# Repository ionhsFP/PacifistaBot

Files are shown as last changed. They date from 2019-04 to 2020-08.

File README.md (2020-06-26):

# PacifistaBot: Kit Humanoide de iniciación
PacifistaBot

Este Kit está pensado para todo aquel que quiera iniciarse en la competición de humanoides. Está diseñado con piezas estandarizadas, baratas, fácil de conseguir y pensado para ser de fácil montaje y programación. Está creado en su totalidad a base de impresión 3D, se programa desde un Arduino Nano y usa una placa controladora fácil de soldar.

Hay que destacar que el robot ha sido diseñado por OPRobots y han liberado las fuentes para que cualquiera pueda replicarlo, modificarlo o seguir desarrollándolo. Aunque su diseño inicial esté inspirado en los robots Pacifistas de la serie One Piece, el diseño es totalmente personalizable ya que tanto las manos y la cabeza, como los detalles decorativos de su pecho y piernas son totalmente modificables e intercambiables para conseguir un robot único.

Mediante este Kit se puede profundizar diferentes niveles de competencias técnicas, de las siguientes áreas STEM:

- Electrónica
- Mecatrónica
- Programación
- Dibujo
- Impresión 3D

El robot pacifistabot originalmente se ha diseñado para controlado por bluetooth. Partiendo de la idea original se ha modificado creando una nueva versión en la que se puede elegir controlarlo mediante bluetooth o mediante wifi (los 2 a la vez no se puede). En la siguiente tabla se puede ver la documentación de cada versión de robot.

| Pacifistabot | Pacifistabot-ESP | Pacifistabot-AlhII |
| --- | --- | --- |
| [Material y Equipos](./montaje/MATERIAL-EQUIPOS.md) | [Material y Equipos](./montaje/MATERIAL-EQUIPOS-ESPyBT.md) | [Material y Equipos](./montaje/MATERIAL-EQUIPOS-AlhII.md) |
| [Montaje y Calibración](./montaje/MONTAJE-CALIBRACION.md) | Montaje y Calibración | Montaje y Calibración |

El coste del material de montaje es inferior a 100 euros y para facilitar poder empezar a montar se ha documentado un listado de Material y Equipos necesarios. Clasificándolos por piezas 3D, componentes mecánicos, componentes electrónicos y equipos de trajo y herramientas.

Para guiar en el proceso de creación de robot, se ha documentado el proceso de Montaje y Calibración. En él se encuentra el proceso de montaje-ajustes mecánicos, montaje electrónico y calibración del robot.

Las especificaciones principales son:

DIMENSIONES

------

- Producto contraido: 320 x 220 x 160 mm
- Producto extendido: 450 x 600 x110 mm

PESO

------

- Producto: 1000 g ~

MATERIALES

------

- Piezas impresas en PLA o ABS
- Tornillos de acero inox.

COMPONENTES ELECTRÓNICOS

------

- 12 Servomotores MG 996R
- Bateria LiFe 6,6V 1100	mAh
- Controladora Arduino Nano
- Módulo Bluetooth hc-05
- Módulo Wifi ESP-01 (solo en Versión Pacifistabot-ESP)

COMUNICACIÓN

------

- Cable mini-Usb
- Bluetooth
- Wifi (solo en Versión Pacifistabot-ESP)
- Programación mediante OTA (Over The Air)(solo en Versión Pacifistabot-ESP)

SOFTWARE

------

- Programación: [Arduino IDE](https://www.arduino.cc/)
- Diseño electrónico: [Kicad](https://www.kicad-pcb.org/)
- Diseño mecánico: [Skeetup](https://www.sketchup.com/)
- Comunicacción: [Putty](https://www.putty.org) / [Arduino IDE](https://www.arduino.cc/) / [ScriptCommunicator](https://github.com/szieke/ScriptCommunicator_serial-terminal) /...
- APP android: [Bluetooth Electronics](https://www.keuwl.com/apps/bluetoothelectronics/) / [BlueTerm](https://play.google.com/store/apps/details?id=es.pymasde.blueterm&hl=en_US) / ...

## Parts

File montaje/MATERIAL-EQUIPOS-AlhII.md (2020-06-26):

# PacifistaBot AlhII: Material y Equipos
PacifistaBot

Dado que es un Kit de iniciación, uno de los puntos más importantes es que el material y equipos necesario para poderse montar no es muy complejo y es fácil de encontrar o de tener disponible. Se va a ir identificando los componentes para que los alumnos y profesores puedan ir gestionando la adquisición de ellos. Este es el materila necesario:

### Piezas 3D

Esta es la lista de piezas que hace falta para poder construir el robot humanoide PacifistaBot. Se necesita imprimir todas las piezas numeradas una sola vez, aunque hay que tener en cuenta que algunas de las piezas tienen varios diseños (por ejemplo la cabeza y las manos) a elegir. Los archivos podemos encontrarlos también en el repositorio de [OPRobots de piezas STL](https://github.com/robotaleh/PacifistaBot/tree/master/stl_files) preparadas para imprimirse en 3D o para poder realizar modificaciones gracias al [formato SketchUp](./../3d_model/PacifistaBot.skp). En este momento faltaría modificar el Torso para poder fijar mediante tornillos la placa PacifistaBot AlhII.

| Nº | Archivo | Descripción | Imagen |
| ---- | :---: | :---: | :---: |
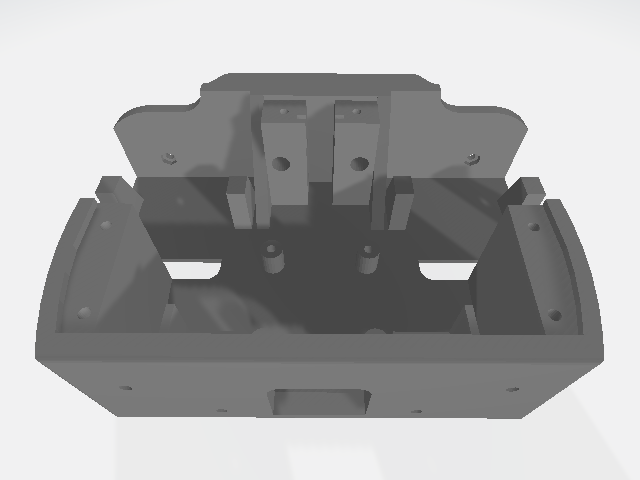
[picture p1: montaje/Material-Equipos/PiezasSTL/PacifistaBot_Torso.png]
| 1 | [PacifistaBot_Torso.stl](../stl_files/PacifistaBot_Torso.stl) | Pecho o caja torácica del robot. |  |
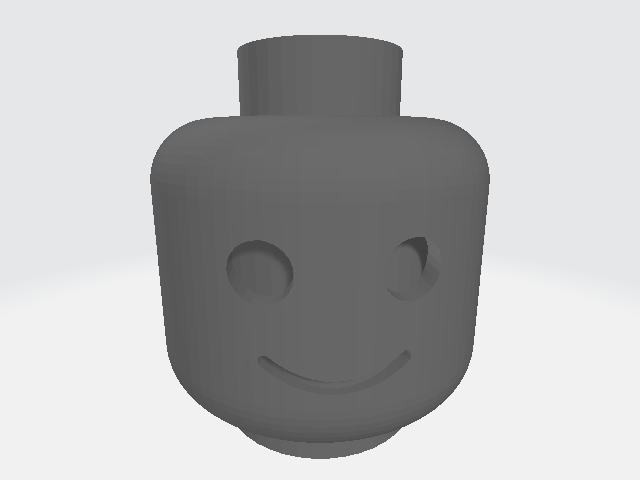
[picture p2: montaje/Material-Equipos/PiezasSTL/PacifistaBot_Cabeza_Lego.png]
| 2 | [PacifistaBot_Cabeza_Lego.stl](../stl_files/PacifistaBot_Cabeza_Lego.stl) | Cabeza hueca con forma muñeco de lego del robot |  |
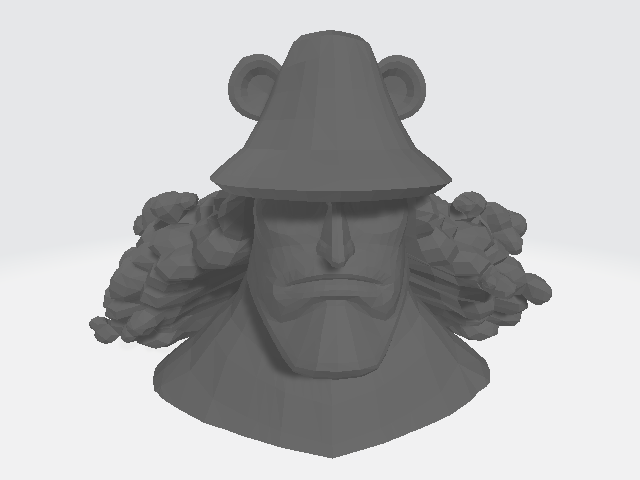
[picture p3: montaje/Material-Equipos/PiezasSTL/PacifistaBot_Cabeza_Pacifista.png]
| 2 | [PacifistaBot_Cabeza_Pacifista.stl](../stl_files/PacifistaBot_Cabeza_Pacifista.stl) | Cabeza maciza con forma de Pacifista de One Piece |  |
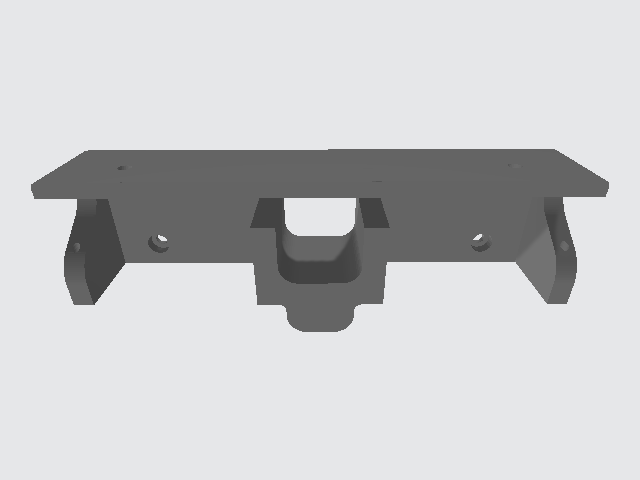
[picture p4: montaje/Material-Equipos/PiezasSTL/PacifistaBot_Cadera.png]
| 3 | [PacifistaBot_Cadera.stl](../stl_files/PacifistaBot_Cadera.stl) | Cadera del robot |   |
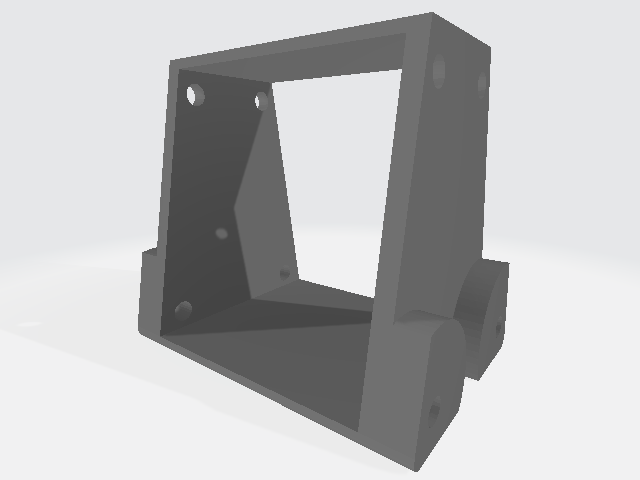
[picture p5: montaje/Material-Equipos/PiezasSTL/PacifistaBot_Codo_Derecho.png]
| 4 | [PacifistaBot_Codo_Derecho.stl](../stl_files/PacifistaBot_Codo_Derecho.stl) | Codo del brazo derecho del robot |  |
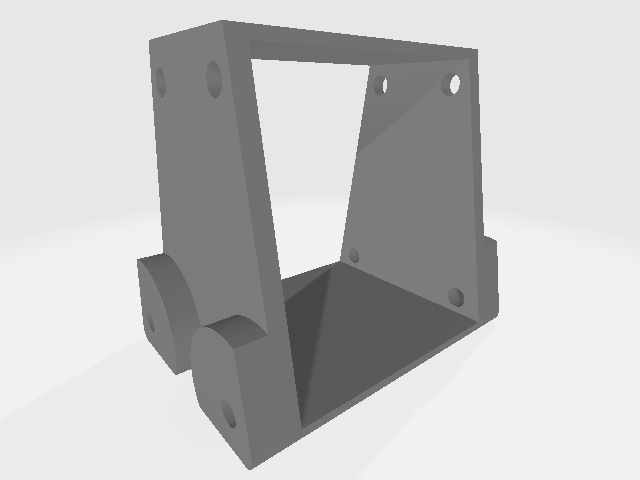
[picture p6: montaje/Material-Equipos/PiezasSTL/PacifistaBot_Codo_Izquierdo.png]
| 5 | [PacifistaBot_Codo_Izquierdo.stl](../stl_files/PacifistaBot_Codo_Izquierdo.stl) | Codo del brazo izquierdo del robot |  |
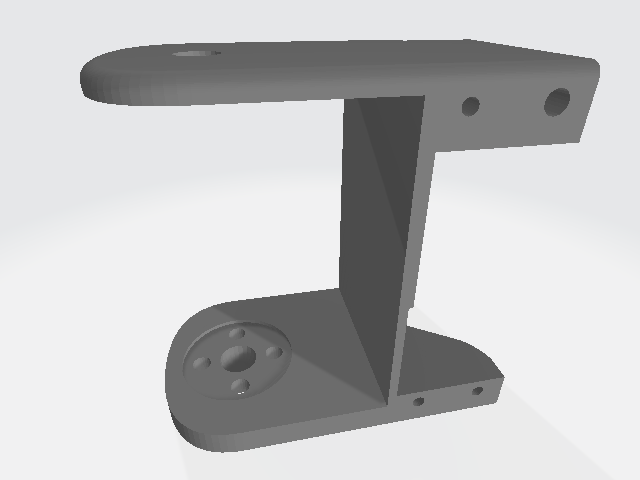
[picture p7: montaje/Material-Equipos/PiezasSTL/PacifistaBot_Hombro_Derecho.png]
| 6 | [PacifistaBot_Hombro_Derecho.stl](../stl_files/PacifistaBot_Hombro_Derecho.stl) | Hombro del brazo derecho del robot |  |
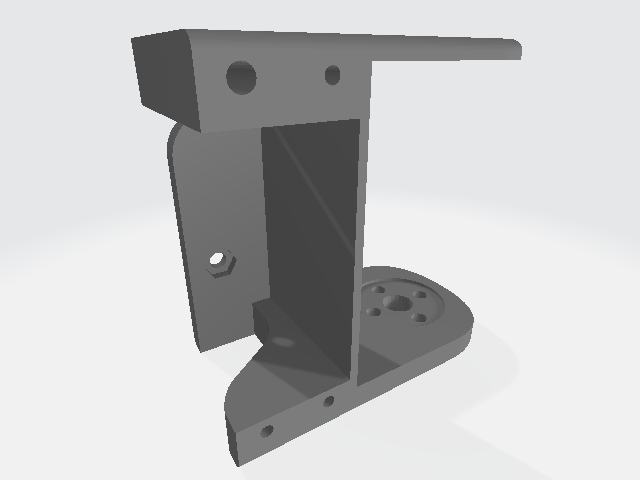
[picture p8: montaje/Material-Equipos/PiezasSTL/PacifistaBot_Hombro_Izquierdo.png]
| 7 | [PacifistaBot_Hombro_Izquierdo.stl](../stl_files/PacifistaBot_Hombro_Izquierdo.stl) | Hombro del brazo izquierdo del robot |  |
| 8 | [PacifistaBot_Ingle_Derecha.stl](../stl_files/PacifistaBot_Ingle_Derecha.stl) | Ingle de la pierna derecha del robot |  |
| 9 | [PacifistaBot_Ingle_Izquierda.stl](../stl_files/PacifistaBot_Ingle_Izquierda.stl) | Ingle de la pierna izquierda del robot |  |
| 10 | [PacifistaBot_Link_Frontal_Inferior_Derecho.stl](../stl_files/PacifistaBot_Link_Frontal_Inferior_Derecho.stl) | Espinilla de la pierna derecha del robot |  |
| 11 | [PacifistaBot_Link_Frontal_Inferior_Izquierdo.stl](../stl_files/PacifistaBot_Link_Frontal_Inferior_Izquierdo.stl) | Espinilla de la pierna izquierda del robot |  |
| 12 | [PacifistaBot_Link_Frontal_Superior_Derecho.stl](../stl_files/PacifistaBot_Link_Frontal_Superior_Derecho.stl) | Cuádriceps femoral del muslo de la pierna derecha del robot  |  |
| 13 | [PacifistaBot_Link_Frontal_Superior_Izquierdo.stl](../stl_files/PacifistaBot_Link_Frontal_Superior_Izquierdo.stl) | Cuádriceps femoral del muslo de la pierna izquierda del robot |  |
| 14 | [PacifistaBot_Link_Mano_Inferior_Frontal_Brazo _Derecho.stl](../stl_files/PacifistaBot_Link_Mano_Inferior_Frontal_Brazo_Derecho.stl) | Antebrazo palmar frontal derecho del robot |  |
| 15 | [PacifistaBot_Link_Mano_Inferior_Frontal_Brazo _Izquierdo.stl](../stl_files/PacifistaBot_Link_Mano_Inferior_Frontal_Brazo_Izquierdo.stl) | Antebrazo palmar frontal izquierdo del robot |  |
| 16 | [PacifistaBot_Link_Mano_Inferior_Trasero_Brazo _Derecho.stl](../stl_files/PacifistaBot_Link_Mano_Inferior_Trasero_Brazo_Derecho.stl) | Antebrazo palmar trasero derecho del robot |  |
| 17 | [PacifistaBot_Link_Mano_Inferior_Trasero_Brazo _Izquierdo.stl](../stl_files/PacifistaBot_Link_Mano_Inferior_Trasero_Brazo_Izquierdo.stl) | Antebrazo palmar trasero izquierdo del robot |  |
| 18 | [PacifistaBot_Link_Mano_Superior_Brazo _Derecho.stl](../stl_files/PacifistaBot_Link_Mano_Superior_Brazo_Derecho.stl) | Antebrazo supinador derecho del robot |  |
| 19 | [PacifistaBot_Link_Mano_Superior_Brazo _Izquierdo.stl](../stl_files/PacifistaBot_Link_Mano_Superior_Brazo_Izquierdo.stl) | Antebrazo supinador izquierdo del robot |  |
| 20 | [PacifistaBot_Link_Servo_Inferior_Frontal_Brazo _Derecho.stl](../stl_files/PacifistaBot_Link_Servo_Inferior_Frontal_Brazo_Derecho.stl) | Triceps frontal del brazo derecho del robot |  |
| 21 | [PacifistaBot_Link_Servo_Inferior_Frontal_Brazo _Izquierdo.stl](../stl_files/PacifistaBot_Link_Servo_Inferior_Frontal_Brazo_Izquierdo.stl) | Triceps frontal del brazo izquierdo del robot |  |
| 22 | [PacifistaBot_Link_Servo_Inferior_Trasero_Brazo _Derecho.stl](../stl_files/PacifistaBot_Link_Servo_Inferior_Trasero_Brazo_Derecho.stl) | Triceps trasero del brazo derecho del robot |  |
| 23 | [PacifistaBot_Link_Servo_Inferior_Trasero_Brazo _Izquierdo.stl](../stl_files/PacifistaBot_Link_Servo_Inferior_Trasero_Brazo_Izquierdo.stl) | Triceps trasero del brazo izquierdo del robot |  |
| 24 | [PacifistaBot_Link_Servo_Superior_Brazo _Derecho.stl](../stl_files/PacifistaBot_Link_Servo_Superior_Brazo_Derecho.stl) | Biceps del brazo derecho del robot |  |
| 25 | [PacifistaBot_Link_Servo_Superior_Brazo _Izquierdo.stl](../stl_files/PacifistaBot_Link_Servo_Superior_Brazo_Izquierdo.stl) | Biceps del brazo izquierdo del robot |  |
| 26 | [PacifistaBot_Link_Trasero_Inferior_Derecho.stl](../stl_files/PacifistaBot_Link_Trasero_Inferior_Derecho.stl) | Gemelo de la pierna derecha del robot |  |
| 27 | [PacifistaBot_Link_Trasero_Inferior_Izquierdo.stl](../stl_files/PacifistaBot_Link_Trasero_Inferior_Izquierdo.stl) | Gemelo de la pierna izquierda del robot |  |
| 28 | [PacifistaBot_Link_Trasero_Superior_Derecho.stl](../stl_files/PacifistaBot_Link_Trasero_Superior_Derecho.stl) | Biceps femoral de la pierna derecha del robot |  |
| 29 | [PacifistaBot_Link_Trasero_Superior_Izquierdo.stl](../stl_files/PacifistaBot_Link_Trasero_Superior_Izquierdo.stl) | Biceps femoral de la pierna izquierda del robot |  |
| 30 | [PacifistaBot_Mano_Lego_Derecha.stl](../stl_files/PacifistaBot_Mano_Lego_Derecha.stl) | Mano derecha con forma de muñeco de lego del robot |  |
| 31 | [PacifistaBot_Mano_Lego_Izquierda.stl](../stl_files/PacifistaBot_Mano_Lego_Izquierda.stl) | Mano izquierda con forma de muñeco de lego del robot |  |
| 30 | [PacifistaBot_Mano_Pacifista_Derecha.stl](../stl_files/PacifistaBot_Mano_Pacifista_Derecha.stl) |  Mano derecha con forma de Pacifista de One Piece del robot  |  |
| 31 | [PacifistaBot_Mano_Pacifista_Izquierda.stl](../stl_files/PacifistaBot_Mano_Pacifista_Izquierda.stl) | Mano izquierda con forma de Pacifista de One Piece del robot |  |
| 32 | [PacifistaBot_Muñeca_Derecha.stl](../stl_files/PacifistaBot_Muñeca_Derecha.stl) | Muñeca de la mano derecha del robot |  |
| 33 | [PacifistaBot_Muñeca_Izquierda.stl](../stl_files/PacifistaBot_Muñeca_Izquierda.stl) | Muñeca de la mano izquierda del robot |  |
| 34 | [PacifistaBot_Pie_Derecho.stl](../stl_files/PacifistaBot_Pie_Derecho.stl) | Pie derecho de la pierna derecha del robot |  |
| 35 | [PacifistaBot_Pie_Izquierdo.stl](../stl_files/PacifistaBot_Pie_Izquierdo.stl) | Pie izquierdo de la pierna derecha del robot |  |
| 36 | [PacifistaBot_Rodilla_Derecha.stl](../stl_files/PacifistaBot_Rodilla_Derecha.stl) | Rodilla de la pierna derecha del robot |  |
| 37 | [PacifistaBot_Rodilla_Izquierda.stl](../stl_files/PacifistaBot_Rodilla_Izquierda.stl) | Rodilla de la pierna izquierda del robot |  |
| 38 | [PacifistaBot_Tobillo_Derecho.stl](../stl_files/PacifistaBot_Tobillo_Derecho.stl) | Tobillo de la pierna derecha del robot |  |
| 39 | [PacifistaBot_Tobillo_Izquierdo.stl](../stl_files/PacifistaBot_Tobillo_Izquierdo.stl) | Tobillo de la pierna izquierda del robot |  |
| 40 | [PacifistaBot_Torso_Tapa.stl](../stl_files/PacifistaBot_Torso_Tapa.stl) | Tapa trasera del torso del robot |  |

### Componentes Mecánicos

A continuación se listan los componentes mecánicos necesarios para la construcción del robot PacifistaBot. Todos los componentes mecánicos y electrónicos son una evolución del robot PacifistaBot diseinado por [OPRobots](https://twitter.com/oprobots) por unos 100 euros, se va a ir identificando los componentes para que los alumnos y profesores puedan ir gestionando la adquisición de ellos. Junto al nombre de cada componente se ha puesto un link orientativo para poder tener una idea de donde comprar el componente. El número de tornillos deben sobrar algunos ya que los valores no están ajustados.

|  Nº  | Nombre/Compra | Descripción | Imagen |
| :--: | :---: | :---: | :---: |
|  12  | [Tornillo M3x8](https://es.aliexpress.com/wholesale?catId=0&initiative_id=SB_20190314011904&isPremium=y&SearchText=allen+m3x8) | Tornillo métrico allen cab. cilíndrica M3x8 |  |
|  33  | [Tornillo M3x10](https://es.aliexpress.com/wholesale?catId=0&initiative_id=SB_20190314011941&isPremium=y&SearchText=allen+m3x10) | Tornillo métrico allen cab. cilíndrica M3x10 |  |
|  35  | [Tornillo M3x16](https://es.aliexpress.com/wholesale?catId=0&initiative_id=SB_20190314012016&isPremium=y&SearchText=allen+m3x16) | Tornillo métrico allen cab. cilíndrica M3x16 |  |
|  10  | [Tornillo M3x25](https://es.aliexpress.com/wholesale?catId=0&initiative_id=SB_20190314012501&isPremium=y&SearchText=allen+m3x25) | Tornillo métrico allen cab. cilíndrica M3x25 (19 mm roscado) |  |
|  12  | [Servomotor](https://es.aliexpress.com/wholesale?catId=0&initiative_id=SB_20190314012523&isPremium=y&SearchText=MG996R) | Servomotor Tower pro MG996R corona metálica |  |
|  12  | [Accesorios servos](https://es.aliexpress.com/wholesale?catId=0&initiative_id=SB_20190314012523&isPremium=y&SearchText=MG996R) | Bolsa de varios accesorios de los servomotores. De la bolsa solo se usan los 4 tornillos roscados para amarrar los servomotres |  |
|  12  | [Disco engranado metálico](https://es.aliexpress.com/wholesale?catId=0&initiative_id=SB_20190314013124&isPremium=y&SearchText=MG996R+Disc) | Disco engranado metálico de los servomotores |  |
|  48  | [Tornillo M3x5](https://es.aliexpress.com/wholesale?catId=0&initiative_id=SB_20190314013124&isPremium=y&SearchText=MG996R+Disc) | Tornillos métricos philips de acero M3x5 para las pletinas metálicas |  |
|  70  | [Tuerca M3](https://es.aliexpress.com/wholesale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) | Tuercas autoblock M3 |  |
|  4 | [Alargadores](https://www.aliexpress.com/wholesale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) | Alargadores 21,5cm para los servomotores |  |

### Componentes Electrónicos

A continuación se listan los componentes electrónicos necesarios para la construcción del robot PacifistaBot-AlhII.  Junto al nombre de cada componente se ha puesto un link orientativo para poder tener una idea de donde comprar el componente. La placa original está diseñada por OPRobots y en esta versión se ha rediseñado adecuándola para hacerla funcionar mediante una Shield de la Alhambra II. La PCB está [diseñada por Don Bosco y Lasalle Berrozpe en Kicad](../pcb_files/Pacifista_AlhII) por lo que cualquiera puede consultar los esquemas y modificarlos. Se ha pasado el [esquema a PDF](../pcb_files/Pacifista_AlhII/Esquema_AlhII.pdf) para poder consultarlo sin necesidad de tener instalado Kicad. Además se han creado los [gerber del circuito Pacifistabot-AlhII](../pcb_files/Pacifista_AlhII/Gerbers) para que cualquiera pueda enviarlos a fabricar a alguno de los fabricantes como [pcbway](https://www.pcbway.com/), [seeedstudio](https://www.seeedstudio.com/fusion.html) ... (no me llevo comisión).

Esta placa puede comunicarse por Bluetooth (en la siguiente versión se espera poner wifi). Por lo que si se tiene claro la manera de comunicarse aparte del módulo, se puede ahorrar ciertos componentes.

|  Nº  | Nombre/Compra | Descripción | Imagen |
| :--: | :---: | :---: | :---: |
|  1 | PCB Pacifistabot AlhII |  Circuito impreso para la electrónica de control del robot.  |  |
|  1 | [Batería](https://hobbyking.com/es_es/zippy-flightmax-1100mah-6-6v-lifepo4-2s1p-receiver-pack.html) | Batería LiFe 2S 1100 mah 10C |  |
|  1 | [Alhambra II](https://alhambrabits.com/alhambra/) | Placa de FPGA Alhambra II |    |
|  1 | [Condensador](https://www.aliexpress.com/wholesale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) | Condensador de 16V y 1000uF |  |
|  1 | [Condensador](https://www.aliexpress.com/wholesale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) | Condensador de 6,3V y 820uF |  |
|  1 | [Bluetooth](https://www.aliexpress.com/wholesale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) (bt) | Módulo Bluetooth HC-05 6 pines y 1 botón |  |
|  1 | [Regulador dc-dc](https://www.aliexpress.com/wholesale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) | Regulador dc-dc MINI-360 con potenciómetro |  |
|  1 | [Tira de 8 pines](https://www.aliexpress.com/wholesale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) | Tira de pines paso 2.54 1x8 negro |  |
|  2 | [Tira de 6 pines](https://www.aliexpress.com/wholesale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) | Tira de pines paso 2.54 1x6 negro |  |
|  5 | [Tira de 6 pines](https://www.aliexpress.com/wholesale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) | Tira de pines paso 2.54 2x6pines negro, rojo y 1x6pines amarillo |    |
|  3 | [Tira de 2 pines](https://www.aliexpress.com/wholesale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) | Tira de pines paso 2.54 2 pines negro, rojo y amarillo |  |
|  1 | [Tira de 4 pines](https://www.aliexpress.com/wholesale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) | Tira de pines paso 2.54 1x4pines negro |  |
|  1 | [Tira de 6 pines hembra](https://www.aliexpress.com/wholesale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) | Tira de pines hembra paso 2.54 1x6pines negro |  |
|  2 | [Regleta 2 contactos](https://es.aliexpress.com/item/33002247818.html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,searchweb201602_,searchweb201603_) | Regleta para PCB con 2 contactos paso 2.54 |  |
|  1 | [Switch](https://es.aliexpress.com/item/33053285882.html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,searchweb201602_9,searchweb201603_53) | Interruptor KCD1 8A-250V |  |
|  2 | [Conectores faston](https://es.aliexpress.com/item/33004981765.html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,searchweb201602_9,searchweb201603_53) | Conector faston cable de 13cm |  |
|  1 | [Carrete de estaño](https://www.aliexpress.com/wholesale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) | Carrete de estaño para soldar |  |
|  1 | [Cable microUSB](https://es.aliexpress.com/wholesale?catId=0&initiative_id=SB_20200626011051&SearchText=microusb+usb) | Cable microUSB |  |

### Equipos y herramientas

Esta es la lista de equipos y herramientas necesarias tanto para el montaje como para el uso y mantenimiento del robot. En la lista aparece lo recomendado algunos no son obligatorios(Tienen un guión "-" en el nombre) o varios tinen la misma función (Tienen un asterisko y un nombre "*1" en el nombre).

|  Nº  | Nombre | Descripción | Imagen |
| :--: | :---: | :---: | :---: |
|  1 | Llave allen | Llave allen de 1,5 |  |
|  1 | Destornillador philips | Destornillador philips de PH00, PH0 y PH1 |  |
|  1 | Alicates *2 | Alicates de punta fina |  |
|  1 | Llave fija *2 |  Llave fija para cabeza hexagonal de 5,5  |  |
|  1 | Estañador | Estañador de 30W y punta fina |  |
|  1 | Tijeras *1 | Tijeras de electricista |  |
|  1 | Cortante *1 | Cortante de pequeño tamaño |  |
|  1 | - Polímetro | Polímetro para medir hasta 10 Vcc |  |
|  1 | PC con Bluetooth | PC con conexión Bluetooth |  |
|  1 | - Protoboard | Protoboard de cualquier tamaño |  |
|  1 |  Cargador de batería | Cargador de baterias LiFe |  |

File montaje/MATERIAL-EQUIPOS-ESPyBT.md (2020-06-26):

# PacifistaBot ESPyBT: Material y Equipos
PacifistaBot

Dado que es un Kit de iniciación, uno de los puntos más importantes es que el material y equipos necesario para poderse montar no es muy complejo y es fácil de encontrar o de tener disponible. Se va a ir identificando los componentes para que los alumnos y profesores puedan ir gestionando la adquisición de ellos. Este es el materila necesario:

### Piezas 3D

Esta es la lista de piezas que hace falta para poder construir el robot humanoide PacifistaBot. Se necesita imprimir todas las piezas numeradas una sola vez, aunque hay que tener en cuenta que algunas de las piezas tienen varios diseños (por ejemplo la cabeza y las manos) a elegir. Los archivos podemos encontrarlos también en el repositorio de [OPRobots de piezas STL](https://github.com/robotaleh/PacifistaBot/tree/master/stl_files) preparadas para imprimirse en 3D o para poder realizar modificaciones gracias al [formato SketchUp](./../3d_model/PacifistaBot.skp).

| Nº | Archivo | Descripción | Imagen |
| ---- | :---: | :---: | :---: |
| 1 | [PacifistaBot_Torso.stl](../stl_files/PacifistaBot_Torso.stl) | Pecho o caja torácica del robot. |  |
| 2 | [PacifistaBot_Cabeza_Lego.stl](../stl_files/PacifistaBot_Cabeza_Lego.stl) | Cabeza hueca con forma muñeco de lego del robot |  |
| 2 | [PacifistaBot_Cabeza_Pacifista.stl](../stl_files/PacifistaBot_Cabeza_Pacifista.stl) | Cabeza maciza con forma de Pacifista de One Piece |  |
| 3 | [PacifistaBot_Cadera.stl](../stl_files/PacifistaBot_Cadera.stl) | Cadera del robot |   |
| 4 | [PacifistaBot_Codo_Derecho.stl](../stl_files/PacifistaBot_Codo_Derecho.stl) | Codo del brazo derecho del robot |  |
| 5 | [PacifistaBot_Codo_Izquierdo.stl](../stl_files/PacifistaBot_Codo_Izquierdo.stl) | Codo del brazo izquierdo del robot |  |
| 6 | [PacifistaBot_Hombro_Derecho.stl](../stl_files/PacifistaBot_Hombro_Derecho.stl) | Hombro del brazo derecho del robot |  |
| 7 | [PacifistaBot_Hombro_Izquierdo.stl](../stl_files/PacifistaBot_Hombro_Izquierdo.stl) | Hombro del brazo izquierdo del robot |  |
| 8 | [PacifistaBot_Ingle_Derecha.stl](../stl_files/PacifistaBot_Ingle_Derecha.stl) | Ingle de la pierna derecha del robot |  |
| 9 | [PacifistaBot_Ingle_Izquierda.stl](../stl_files/PacifistaBot_Ingle_Izquierda.stl) | Ingle de la pierna izquierda del robot |  |
| 10 | [PacifistaBot_Link_Frontal_Inferior_Derecho.stl](../stl_files/PacifistaBot_Link_Frontal_Inferior_Derecho.stl) | Espinilla de la pierna derecha del robot |  |
| 11 | [PacifistaBot_Link_Frontal_Inferior_Izquierdo.stl](../stl_files/PacifistaBot_Link_Frontal_Inferior_Izquierdo.stl) | Espinilla de la pierna izquierda del robot |  |
| 12 | [PacifistaBot_Link_Frontal_Superior_Derecho.stl](../stl_files/PacifistaBot_Link_Frontal_Superior_Derecho.stl) | Cuádriceps femoral del muslo de la pierna derecha del robot  |  |
| 13 | [PacifistaBot_Link_Frontal_Superior_Izquierdo.stl](../stl_files/PacifistaBot_Link_Frontal_Superior_Izquierdo.stl) | Cuádriceps femoral del muslo de la pierna izquierda del robot |  |
| 14 | [PacifistaBot_Link_Mano_Inferior_Frontal_Brazo _Derecho.stl](../stl_files/PacifistaBot_Link_Mano_Inferior_Frontal_Brazo_Derecho.stl) | Antebrazo palmar frontal derecho del robot |  |
| 15 | [PacifistaBot_Link_Mano_Inferior_Frontal_Brazo _Izquierdo.stl](../stl_files/PacifistaBot_Link_Mano_Inferior_Frontal_Brazo_Izquierdo.stl) | Antebrazo palmar frontal izquierdo del robot |  |
| 16 | [PacifistaBot_Link_Mano_Inferior_Trasero_Brazo _Derecho.stl](../stl_files/PacifistaBot_Link_Mano_Inferior_Trasero_Brazo_Derecho.stl) | Antebrazo palmar trasero derecho del robot |  |
| 17 | [PacifistaBot_Link_Mano_Inferior_Trasero_Brazo _Izquierdo.stl](../stl_files/PacifistaBot_Link_Mano_Inferior_Trasero_Brazo_Izquierdo.stl) | Antebrazo palmar trasero izquierdo del robot |  |
| 18 | [PacifistaBot_Link_Mano_Superior_Brazo _Derecho.stl](../stl_files/PacifistaBot_Link_Mano_Superior_Brazo_Derecho.stl) | Antebrazo supinador derecho del robot |  |
| 19 | [PacifistaBot_Link_Mano_Superior_Brazo _Izquierdo.stl](../stl_files/PacifistaBot_Link_Mano_Superior_Brazo_Izquierdo.stl) | Antebrazo supinador izquierdo del robot |  |
| 20 | [PacifistaBot_Link_Servo_Inferior_Frontal_Brazo _Derecho.stl](../stl_files/PacifistaBot_Link_Servo_Inferior_Frontal_Brazo_Derecho.stl) | Triceps frontal del brazo derecho del robot |  |
| 21 | [PacifistaBot_Link_Servo_Inferior_Frontal_Brazo _Izquierdo.stl](../stl_files/PacifistaBot_Link_Servo_Inferior_Frontal_Brazo_Izquierdo.stl) | Triceps frontal del brazo izquierdo del robot |  |
| 22 | [PacifistaBot_Link_Servo_Inferior_Trasero_Brazo _Derecho.stl](../stl_files/PacifistaBot_Link_Servo_Inferior_Trasero_Brazo_Derecho.stl) | Triceps trasero del brazo derecho del robot |  |
| 23 | [PacifistaBot_Link_Servo_Inferior_Trasero_Brazo _Izquierdo.stl](../stl_files/PacifistaBot_Link_Servo_Inferior_Trasero_Brazo_Izquierdo.stl) | Triceps trasero del brazo izquierdo del robot |  |
| 24 | [PacifistaBot_Link_Servo_Superior_Brazo _Derecho.stl](../stl_files/PacifistaBot_Link_Servo_Superior_Brazo_Derecho.stl) | Biceps del brazo derecho del robot |  |
| 25 | [PacifistaBot_Link_Servo_Superior_Brazo _Izquierdo.stl](../stl_files/PacifistaBot_Link_Servo_Superior_Brazo_Izquierdo.stl) | Biceps del brazo izquierdo del robot |  |
| 26 | [PacifistaBot_Link_Trasero_Inferior_Derecho.stl](../stl_files/PacifistaBot_Link_Trasero_Inferior_Derecho.stl) | Gemelo de la pierna derecha del robot |  |
| 27 | [PacifistaBot_Link_Trasero_Inferior_Izquierdo.stl](../stl_files/PacifistaBot_Link_Trasero_Inferior_Izquierdo.stl) | Gemelo de la pierna izquierda del robot |  |
| 28 | [PacifistaBot_Link_Trasero_Superior_Derecho.stl](../stl_files/PacifistaBot_Link_Trasero_Superior_Derecho.stl) | Biceps femoral de la pierna derecha del robot |  |
| 29 | [PacifistaBot_Link_Trasero_Superior_Izquierdo.stl](../stl_files/PacifistaBot_Link_Trasero_Superior_Izquierdo.stl) | Biceps femoral de la pierna izquierda del robot |  |
| 30 | [PacifistaBot_Mano_Lego_Derecha.stl](../stl_files/PacifistaBot_Mano_Lego_Derecha.stl) | Mano derecha con forma de muñeco de lego del robot |  |
| 31 | [PacifistaBot_Mano_Lego_Izquierda.stl](../stl_files/PacifistaBot_Mano_Lego_Izquierda.stl) | Mano izquierda con forma de muñeco de lego del robot |  |
| 30 | [PacifistaBot_Mano_Pacifista_Derecha.stl](../stl_files/PacifistaBot_Mano_Pacifista_Derecha.stl) |  Mano derecha con forma de Pacifista de One Piece del robot  |  |
| 31 | [PacifistaBot_Mano_Pacifista_Izquierda.stl](../stl_files/PacifistaBot_Mano_Pacifista_Izquierda.stl) | Mano izquierda con forma de Pacifista de One Piece del robot |  |
| 32 | [PacifistaBot_Muñeca_Derecha.stl](../stl_files/PacifistaBot_Muñeca_Derecha.stl) | Muñeca de la mano derecha del robot |  |
| 33 | [PacifistaBot_Muñeca_Izquierda.stl](../stl_files/PacifistaBot_Muñeca_Izquierda.stl) | Muñeca de la mano izquierda del robot |  |
| 34 | [PacifistaBot_Pie_Derecho.stl](../stl_files/PacifistaBot_Pie_Derecho.stl) | Pie derecho de la pierna derecha del robot |  |
| 35 | [PacifistaBot_Pie_Izquierdo.stl](../stl_files/PacifistaBot_Pie_Izquierdo.stl) | Pie izquierdo de la pierna derecha del robot |  |
| 36 | [PacifistaBot_Rodilla_Derecha.stl](../stl_files/PacifistaBot_Rodilla_Derecha.stl) | Rodilla de la pierna derecha del robot |  |
| 37 | [PacifistaBot_Rodilla_Izquierda.stl](../stl_files/PacifistaBot_Rodilla_Izquierda.stl) | Rodilla de la pierna izquierda del robot |  |
| 38 | [PacifistaBot_Tobillo_Derecho.stl](../stl_files/PacifistaBot_Tobillo_Derecho.stl) | Tobillo de la pierna derecha del robot |  |
| 39 | [PacifistaBot_Tobillo_Izquierdo.stl](../stl_files/PacifistaBot_Tobillo_Izquierdo.stl) | Tobillo de la pierna izquierda del robot |  |
| 40 | [PacifistaBot_Torso_Tapa.stl](../stl_files/PacifistaBot_Torso_Tapa.stl) | Tapa trasera del torso del robot |  |

### Componentes Mecánicos

A continuación se listan los componentes mecánicos necesarios para la construcción del robot PacifistaBot. Todos los componentes mecánicos y electrónicos han sido suministrados por [OPRobots](https://twitter.com/oprobots) por unos 100 euros, se va a ir identificando los componentes para que los alumnos y profesores puedan ir gestionando la adquisición de ellos. Junto al nombre de cada componente se ha puesto un link orientativo para poder tener una idea de donde comprar el componente. El número de tornillos deben sobrar algunos ya que los valores no están ajustados.

|  Nº  | Nombre/Compra | Descripción | Imagen |
| :--: | :---: | :---: | :---: |
|  12  | [Tornillo M3x8](https://es.aliexpress.com/wholesale?catId=0&initiative_id=SB_20190314011904&isPremium=y&SearchText=allen+m3x8) | Tornillo métrico allen cab. cilíndrica M3x8 |  |
|  33  | [Tornillo M3x10](https://es.aliexpress.com/wholesale?catId=0&initiative_id=SB_20190314011941&isPremium=y&SearchText=allen+m3x10) | Tornillo métrico allen cab. cilíndrica M3x10 |  |
|  35  | [Tornillo M3x16](https://es.aliexpress.com/wholesale?catId=0&initiative_id=SB_20190314012016&isPremium=y&SearchText=allen+m3x16) | Tornillo métrico allen cab. cilíndrica M3x16 |  |
|  10  | [Tornillo M3x25](https://es.aliexpress.com/wholesale?catId=0&initiative_id=SB_20190314012501&isPremium=y&SearchText=allen+m3x25) | Tornillo métrico allen cab. cilíndrica M3x25 (19 mm roscado) |  |
|  12  | [Servomotor](https://es.aliexpress.com/wholesale?catId=0&initiative_id=SB_20190314012523&isPremium=y&SearchText=MG996R) | Servomotor Tower pro MG996R corona metálica |  |
|  12  | [Accesorios servos](https://es.aliexpress.com/wholesale?catId=0&initiative_id=SB_20190314012523&isPremium=y&SearchText=MG996R) | Bolsa de varios accesorios de los servomotores. De la bolsa solo se usan los 4 tornillos roscados para amarrar los servomotres |  |
|  12  | [Disco engranado metálico](https://es.aliexpress.com/wholesale?catId=0&initiative_id=SB_20190314013124&isPremium=y&SearchText=MG996R+Disc) | Disco engranado metálico de los servomotores |  |
|  48  | [Tornillo M3x5](https://es.aliexpress.com/wholesale?catId=0&initiative_id=SB_20190314013124&isPremium=y&SearchText=MG996R+Disc) | Tornillos métricos philips de acero M3x5 para las pletinas metálicas |  |
|  70  | [Tuerca M3](https://es.aliexpress.com/wholesale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) | Tuercas autoblock M3 |  |
|  4 | [Alargadores](https://www.aliexpress.com/wholesale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) | Alargadores 21,5cm para los servomotores |  |

### Componentes Electrónicos

A continuación se listan los componentes electrónicos necesarios para la construcción del robot PacifistaBot-ESP.  Junto al nombre de cada componente se ha puesto un link orientativo para poder tener una idea de donde comprar el componente. La placa original está diseñada por OPRobots y en esta versión se le han metido ciertas mejoras electrónica. La PCB está [diseñada por Don Bosco y Lasalle Berrozpe en Kicad](../pcb_files/Pacifista_ESP) por lo que cualquiera puede consultar los esquemas y modificarlos. Se ha pasado el [esquema a PDF](../pcb_files/Pacifista_ESP/Esquema.pdf) para poder consultarlo sin necesidad de tener instalado Kicad. Además se han creado los [gerber del circuito Pacifistabot-ESP](../pcb_files/Pacifista_ESP/gerbers) para que cualquiera pueda enviarlos a fabricar a alguno de los fabricantes como [pcbway](https://www.pcbway.com/), [seeedstudio](https://www.seeedstudio.com/fusion.html) ... (no me llevo comisión).

Esta placa puede comunicarse por Bluetooth o por Wifi (No se puede comunicar las 2 a la vez). Por lo que si se tiene claro la manera de comunicarse aparte del módulo, se puede ahorrar ciertos componentes. Para identificar los componentes necesarios para comunicarse por Bluetooth o Wifi se ha añadido entre paréntesis las iniciales bt o w.

|  Nº  | Nombre/Compra | Descripción | Imagen |
| :--: | :---: | :---: | :---: |
|  1 | [PCB Pacifistabot ESP-BT](../pcb_files/Pacifista_ESP/gerbers) |  Circuito impreso para la electrónica de control del robot.  | |
|  1 | [Batería](https://hobbyking.com/es_es/zippy-flightmax-1100mah-6-6v-lifepo4-2s1p-receiver-pack.html) | Batería LiFe 2S 1100 mah 10C |  |
|  1 | [Arduino nano](https://www.aliexpress.com/wholesale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) | Placa Arduino nano con los pines de conexión |  |
|  1 | [Condensador](https://www.aliexpress.com/wholesale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) | Condensador de 16V y 1000uF |  |
|  1 | [Condensador](https://www.aliexpress.com/wholesale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) | Condensador de 6,3V y 820uF |  |
|  1 | [Condensador](https://es.aliexpress.com/wholesale?catId=0&initiative_id=SB_20200114034955&SearchText=condensador+1206+330nF) (w) | Condensador de 6,3V y 330nF |  |
|  1 | [Bluetooth](https://www.aliexpress.com/wholesale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) (bt) | Módulo Bluetooth HC-05 6 pines y 1 botón |  |
|  1 | [Wifi](<https://es.aliexpress.com/item/32948119527.html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,searchweb201602_9,searchweb201603_53>) (w) | Módulo Wifi ESP8266 ESP-01S |  |
|  2 | [Tira de 4 pines hembra](https://www.aliexpress.com/wholesale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) (w) | Tira de pines hembra paso 2.54 2x4pines negro |  |
|  1 | [Regulador dc-dc](https://www.aliexpress.com/wholesale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) | Regulador dc-dc MINI-360 con potenciómetro |  |
|  1 | [Regulador dc-dc](https://es.aliexpress.com/item/32855727753.html?spm=a2g0s.9042311.0.0.6fe163c0i47Cze) (w) | Regulador ASM1117 3,3v con SOT-223 |   |
|  5 | [Tira de 6 pines](https://www.aliexpress.com/wholesale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) | Tira de pines paso 2.54 2x6pines negro, rojo y 1x6pines amarillo |    |
|  1 | [Tira de 9 pines](https://www.aliexpress.com/wholesale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) | Tira de pines paso 2.54 1x9pines amarillo |    |
|  3 | [Tira de 2 pines](https://www.aliexpress.com/wholesale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) | Tira de pines paso 2.54 1x2pines negro, rojo, blanco |    |
|  1 | [Tira de 4 pines](https://www.aliexpress.com/wholesale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) | Tira de pines paso 2.54 1x4pines negro |    |
|  2 | [Tira de 15 pines hembra](https://www.aliexpress.com/wholesale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) | Tira de pines hembra paso 2.54 1x15pines negro |   |
|  1 | [Tira de 6 pines hembra](https://www.aliexpress.com/wholesale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) (bt) | Tira de pines hembra paso 2.54 1x6pines negro |  |
|  2 | [Resistencias](https://www.aliexpress.com/wholesale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) | Resistencia 10kΩ con tolerancia %1 y potencia 1/4 W |  |
|  2 | [Resistencias](https://www.aliexpress.com/wholesale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) | Resistencia 20kΩ con tolerancia %1 y potencia 1/4 W |  |
|  3 | Resistencias (w) | Resistencia 10kΩ SMD 1206 |  |
|  1 | [Switch](https://es.aliexpress.com/item/33053285882.html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,searchweb201602_9,searchweb201603_53) | Interruptor KCD1 8A-250V |  |
|  2 | [Conectores faston](https://es.aliexpress.com/item/33004981765.html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,searchweb201602_9,searchweb201603_53) | Conector faston cable de 13cm |  |
|  1 | [Carrete de estaño](https://www.aliexpress.com/wholesale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) | Carrete de estaño para soldar |  |
|  1 | [Cable miniUSB](https://www.aliexpress.com/wholesale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) | Cable USB a miniUSB |  |

### Equipos y herramientas

Esta es la lista de equipos y herramientas necesarias tanto para el montaje como para el uso y mantenimiento del robot. En la lista aparece lo recomendado algunos no son obligatorios(Tienen un guión "-" en el nombre) o varios tinen la misma función (Tienen un asterisko y un nombre "*1" en el nombre).

|  Nº  | Nombre | Descripción | Imagen |
| :--: | :---: | :---: | :---: |
|  1 | Llave allen | Llave allen de 1,5 |  |
|  1 | Destornillador philips | Destornillador philips de PH00, PH0 y PH1 |  |
|  1 | Alicates *2 | Alicates de punta fina |  |
|  1 | Llave fija *2 |  Llave fija para cabeza hexagonal de 5,5  |  |
|  1 | Estañador | Estañador de 30W y punta fina |  |
|  1 | Tijeras *1 | Tijeras de electricista |  |
|  1 | Cortante *1 | Cortante de pequeño tamaño |  |
|  1 | - Polímetro | Polímetro para medir hasta 10 Vcc |  |
|  1 | PC con Bluetooth | PC con conexión Bluetooth |  |
|  1 | - Protoboard | Protoboard de cualquier tamaño |  |
|  1 |  Cargador de batería | Cargador de baterias LiFe |  |

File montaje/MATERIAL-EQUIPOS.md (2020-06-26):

# PacifistaBot: Material y Equipos
PacifistaBot

Dado que es un Kit de iniciación, uno de los puntos más importantes es que el material y equipos necesario para poderse montar no es muy complejo y es fácil de encontrar o de tener disponible. Este es el materila necesario:

### Piezas 3D

Esta es la lista de piezas que hace falta para poder construir el robot humanoide PacifistaBot. Se necesita imprimir todas las piezas numeradas una sola vez, aunque hay que tener en cuenta que algunas de las piezas tienen varios diseños (por ejemplo la cabeza y las manos) a elegir. Los archivos podemos encontrarlos también en el repositorio de [OPRobots de piezas STL](https://github.com/robotaleh/PacifistaBot/tree/master/stl_files) preparadas para imprimirse en 3D o para poder realizar modificaciones gracias al [formato SketchUp](./../3d_model/PacifistaBot.skp).

| Nº | Archivo | Descripción | Imagen |
| ---- | :---: | :---: | :---: |
| 1 | [PacifistaBot_Torso.stl](../stl_files/PacifistaBot_Torso.stl) | Pecho o caja torácica del robot. |  |
| 2 | [PacifistaBot_Cabeza_Lego.stl](../stl_files/PacifistaBot_Cabeza_Lego.stl) | Cabeza hueca con forma muñeco de lego del robot |  |
| 2 | [PacifistaBot_Cabeza_Pacifista.stl](../stl_files/PacifistaBot_Cabeza_Pacifista.stl) | Cabeza maciza con forma de Pacifista de One Piece |  |
| 3 | [PacifistaBot_Cadera.stl](../stl_files/PacifistaBot_Cadera.stl) | Cadera del robot |   |
| 4 | [PacifistaBot_Codo_Derecho.stl](../stl_files/PacifistaBot_Codo_Derecho.stl) | Codo del brazo derecho del robot |  |
| 5 | [PacifistaBot_Codo_Izquierdo.stl](../stl_files/PacifistaBot_Codo_Izquierdo.stl) | Codo del brazo izquierdo del robot |  |
| 6 | [PacifistaBot_Hombro_Derecho.stl](../stl_files/PacifistaBot_Hombro_Derecho.stl) | Hombro del brazo derecho del robot |  |
| 7 | [PacifistaBot_Hombro_Izquierdo.stl](../stl_files/PacifistaBot_Hombro_Izquierdo.stl) | Hombro del brazo izquierdo del robot |  |
| 8 | [PacifistaBot_Ingle_Derecha.stl](../stl_files/PacifistaBot_Ingle_Derecha.stl) | Ingle de la pierna derecha del robot |  |
| 9 | [PacifistaBot_Ingle_Izquierda.stl](../stl_files/PacifistaBot_Ingle_Izquierda.stl) | Ingle de la pierna izquierda del robot |  |
| 10 | [PacifistaBot_Link_Frontal_Inferior_Derecho.stl](../stl_files/PacifistaBot_Link_Frontal_Inferior_Derecho.stl) | Espinilla de la pierna derecha del robot |  |
| 11 | [PacifistaBot_Link_Frontal_Inferior_Izquierdo.stl](../stl_files/PacifistaBot_Link_Frontal_Inferior_Izquierdo.stl) | Espinilla de la pierna izquierda del robot |  |
| 12 | [PacifistaBot_Link_Frontal_Superior_Derecho.stl](../stl_files/PacifistaBot_Link_Frontal_Superior_Derecho.stl) | Cuádriceps femoral del muslo de la pierna derecha del robot  |  |
| 13 | [PacifistaBot_Link_Frontal_Superior_Izquierdo.stl](../stl_files/PacifistaBot_Link_Frontal_Superior_Izquierdo.stl) | Cuádriceps femoral del muslo de la pierna izquierda del robot |  |
| 14 | [PacifistaBot_Link_Mano_Inferior_Frontal_Brazo _Derecho.stl](../stl_files/PacifistaBot_Link_Mano_Inferior_Frontal_Brazo_Derecho.stl) | Antebrazo palmar frontal derecho del robot |  |
| 15 | [PacifistaBot_Link_Mano_Inferior_Frontal_Brazo _Izquierdo.stl](../stl_files/PacifistaBot_Link_Mano_Inferior_Frontal_Brazo_Izquierdo.stl) | Antebrazo palmar frontal izquierdo del robot |  |
| 16 | [PacifistaBot_Link_Mano_Inferior_Trasero_Brazo _Derecho.stl](../stl_files/PacifistaBot_Link_Mano_Inferior_Trasero_Brazo_Derecho.stl) | Antebrazo palmar trasero derecho del robot |  |
| 17 | [PacifistaBot_Link_Mano_Inferior_Trasero_Brazo _Izquierdo.stl](../stl_files/PacifistaBot_Link_Mano_Inferior_Trasero_Brazo_Izquierdo.stl) | Antebrazo palmar trasero izquierdo del robot |  |
| 18 | [PacifistaBot_Link_Mano_Superior_Brazo _Derecho.stl](../stl_files/PacifistaBot_Link_Mano_Superior_Brazo_Derecho.stl) | Antebrazo supinador derecho del robot |  |
| 19 | [PacifistaBot_Link_Mano_Superior_Brazo _Izquierdo.stl](../stl_files/PacifistaBot_Link_Mano_Superior_Brazo_Izquierdo.stl) | Antebrazo supinador izquierdo del robot |  |
| 20 | [PacifistaBot_Link_Servo_Inferior_Frontal_Brazo _Derecho.stl](../stl_files/PacifistaBot_Link_Servo_Inferior_Frontal_Brazo_Derecho.stl) | Triceps frontal del brazo derecho del robot |  |
| 21 | [PacifistaBot_Link_Servo_Inferior_Frontal_Brazo _Izquierdo.stl](../stl_files/PacifistaBot_Link_Servo_Inferior_Frontal_Brazo_Izquierdo.stl) | Triceps frontal del brazo izquierdo del robot |  |
| 22 | [PacifistaBot_Link_Servo_Inferior_Trasero_Brazo _Derecho.stl](../stl_files/PacifistaBot_Link_Servo_Inferior_Trasero_Brazo_Derecho.stl) | Triceps trasero del brazo derecho del robot |  |
| 23 | [PacifistaBot_Link_Servo_Inferior_Trasero_Brazo _Izquierdo.stl](../stl_files/PacifistaBot_Link_Servo_Inferior_Trasero_Brazo_Izquierdo.stl) | Triceps trasero del brazo izquierdo del robot |  |
| 24 | [PacifistaBot_Link_Servo_Superior_Brazo _Derecho.stl](../stl_files/PacifistaBot_Link_Servo_Superior_Brazo_Derecho.stl) | Biceps del brazo derecho del robot |  |
| 25 | [PacifistaBot_Link_Servo_Superior_Brazo _Izquierdo.stl](../stl_files/PacifistaBot_Link_Servo_Superior_Brazo_Izquierdo.stl) | Biceps del brazo izquierdo del robot |  |
| 26 | [PacifistaBot_Link_Trasero_Inferior_Derecho.stl](../stl_files/PacifistaBot_Link_Trasero_Inferior_Derecho.stl) | Gemelo de la pierna derecha del robot |  |
| 27 | [PacifistaBot_Link_Trasero_Inferior_Izquierdo.stl](../stl_files/PacifistaBot_Link_Trasero_Inferior_Izquierdo.stl) | Gemelo de la pierna izquierda del robot |  |
| 28 | [PacifistaBot_Link_Trasero_Superior_Derecho.stl](../stl_files/PacifistaBot_Link_Trasero_Superior_Derecho.stl) | Biceps femoral de la pierna derecha del robot |  |
| 29 | [PacifistaBot_Link_Trasero_Superior_Izquierdo.stl](../stl_files/PacifistaBot_Link_Trasero_Superior_Izquierdo.stl) | Biceps femoral de la pierna izquierda del robot |  |
| 30 | [PacifistaBot_Mano_Lego_Derecha.stl](../stl_files/PacifistaBot_Mano_Lego_Derecha.stl) | Mano derecha con forma de muñeco de lego del robot |  |
| 31 | [PacifistaBot_Mano_Lego_Izquierda.stl](../stl_files/PacifistaBot_Mano_Lego_Izquierda.stl) | Mano izquierda con forma de muñeco de lego del robot |  |
| 30 | [PacifistaBot_Mano_Pacifista_Derecha.stl](../stl_files/PacifistaBot_Mano_Pacifista_Derecha.stl) |  Mano derecha con forma de Pacifista de One Piece del robot  |  |
| 31 | [PacifistaBot_Mano_Pacifista_Izquierda.stl](../stl_files/PacifistaBot_Mano_Pacifista_Izquierda.stl) | Mano izquierda con forma de Pacifista de One Piece del robot |  |
| 32 | [PacifistaBot_Muñeca_Derecha.stl](../stl_files/PacifistaBot_Muñeca_Derecha.stl) | Muñeca de la mano derecha del robot |  |
| 33 | [PacifistaBot_Muñeca_Izquierda.stl](../stl_files/PacifistaBot_Muñeca_Izquierda.stl) | Muñeca de la mano izquierda del robot |  |
| 34 | [PacifistaBot_Pie_Derecho.stl](../stl_files/PacifistaBot_Pie_Derecho.stl) | Pie derecho de la pierna derecha del robot |  |
| 35 | [PacifistaBot_Pie_Izquierdo.stl](../stl_files/PacifistaBot_Pie_Izquierdo.stl) | Pie izquierdo de la pierna derecha del robot |  |
| 36 | [PacifistaBot_Rodilla_Derecha.stl](../stl_files/PacifistaBot_Rodilla_Derecha.stl) | Rodilla de la pierna derecha del robot |  |
| 37 | [PacifistaBot_Rodilla_Izquierda.stl](../stl_files/PacifistaBot_Rodilla_Izquierda.stl) | Rodilla de la pierna izquierda del robot |  |
| 38 | [PacifistaBot_Tobillo_Derecho.stl](../stl_files/PacifistaBot_Tobillo_Derecho.stl) | Tobillo de la pierna derecha del robot |  |
| 39 | [PacifistaBot_Tobillo_Izquierdo.stl](../stl_files/PacifistaBot_Tobillo_Izquierdo.stl) | Tobillo de la pierna izquierda del robot |  |
| 40 | [PacifistaBot_Torso_Tapa.stl](../stl_files/PacifistaBot_Torso_Tapa.stl) | Tapa trasera del torso del robot |  |

### Componentes Mecánicos

A continuación se listan los componentes mecánicos necesarios para la construcción del robot PacifistaBot. Todos los componentes mecánicos y electrónicos han sido suministrados por [OPRobots](https://twitter.com/oprobots) por unos 100 euros, se va a ir identificando los componentes para que los alumnos y profesores puedan ir gestionando la adquisición de ellos. Junto al nombre de cada componente se ha puesto un link orientativo para poder tener una idea de donde comprar el componente. El número de tornillos deben sobrar algunos ya que los valores no están ajustados.

|  Nº  | Nombre/Compra | Descripción | Imagen |
| :--: | :---: | :---: | :---: |
|  12  | [Tornillo M3x8](https://es.aliexpress.com/wholesale?catId=0&initiative_id=SB_20190314011904&isPremium=y&SearchText=allen+m3x8) | Tornillo métrico allen cab. cilíndrica M3x8 |  |
|  33  | [Tornillo M3x10](https://es.aliexpress.com/wholesale?catId=0&initiative_id=SB_20190314011941&isPremium=y&SearchText=allen+m3x10) | Tornillo métrico allen cab. cilíndrica M3x10 |  |
|  35  | [Tornillo M3x16](https://es.aliexpress.com/wholesale?catId=0&initiative_id=SB_20190314012016&isPremium=y&SearchText=allen+m3x16) | Tornillo métrico allen cab. cilíndrica M3x16 |  |
|  10  | [Tornillo M3x25](https://es.aliexpress.com/wholesale?catId=0&initiative_id=SB_20190314012501&isPremium=y&SearchText=allen+m3x25) | Tornillo métrico allen cab. cilíndrica M3x25 (19 mm roscado) |  |
|  12  | [Servomotor](https://es.aliexpress.com/wholesale?catId=0&initiative_id=SB_20190314012523&isPremium=y&SearchText=MG996R) | Servomotor Tower pro MG996R corona metálica |  |
|  12  | [Accesorios servos](https://es.aliexpress.com/wholesale?catId=0&initiative_id=SB_20190314012523&isPremium=y&SearchText=MG996R) | Bolsa de varios accesorios de los servomotores. De la bolsa solo se usan los 4 tornillos roscados para amarrar los servomotres |  |
|  12  | [Disco engranado metálico](https://es.aliexpress.com/wholesale?catId=0&initiative_id=SB_20190314013124&isPremium=y&SearchText=MG996R+Disc) | Disco engranado metálico de los servomotores |  |
|  48  | [Tornillo M3x5](https://es.aliexpress.com/wholesale?catId=0&initiative_id=SB_20190314013124&isPremium=y&SearchText=MG996R+Disc) | Tornillos métricos philips de acero M3x5 para las pletinas metálicas |  |
|  70  | [Tuerca M3](https://es.aliexpress.com/wholesale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) | Tuercas autoblock M3 |  |
|  4 | [Alargadores](https://www.aliexpress.com/wholesale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) | Alargadores 21,5cm para los servomotores |  |
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

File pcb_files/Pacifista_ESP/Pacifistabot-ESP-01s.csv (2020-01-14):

Id | Identificador | Empaquetado | Cantidad | Identificación | Suministrador y ref
1 | ,,, | MountingHole_3.2mm_M3_Pad_Via | 4 | MountingHole_3.2mm_M3_Pad_Via
2 | U3 | PinHeader_2x04_P2.54mm_Vertical | 1 | ESP-01v090
3 | A1 | arduino_nano | 1 | Arduino_Nano
4 | C1 | CP_Radial_D8.0mm_P3.80mm | 1 | 1000u 16v
5 | C2 | CP_Radial_D10.0mm_P5.00mm | 1 | 820u 6,3v
6 | J1,J2 | SolderWirePad_single_1-5mmDrill | 2 | Conn_01x01
7 | J5,J6,J7,J8,J4 | Pin_Header_Straight_1x06_Pitch2.54mm | 5 | Conn_01x06
8 | J10,J11 | Pin_Header_Straight_1x03_Pitch2.54mm | 2 | Conn_01x03
9 | R2,R4 | R_Axial_DIN0207_L6.3mm_D2.5mm_P7.62mm_Horizontal | 2 | 10K
10 | R3,R5 | R_Axial_DIN0207_L6.3mm_D2.5mm_P7.62mm_Horizontal | 2 | 20K
11 | U1 | Step_down_chino | 1 | Step_down_chino
12 | U2 | SOT-223-3_TabPin2 | 1 | AMS1117
13 | R1,R6,R7 | R_1206_3216Metric_Pad1.42x1.75mm_HandSolder | 3 | 10K
14 | J3 | PinHeader_1x09_P2.54mm_Vertical | 1 | Conn_01x09
15 | J9 | PinSocket_1x06_P2.54mm_Vertical | 1 | Conn_01x06
16 | C3 | C_1206_3216Metric_Pad1.42x1.75mm_HandSolder | 1 | 330nF1
17 |  | opr_circulo_6x6_v1 | 1
18 | G*** | LogoDB | 1 | LOGO
19 | G*** | lsblogo | 1 | LOGO

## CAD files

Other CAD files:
pcb_files/Pacifista_TinyFPGA/Pacifista_TinyFPGA-B_SilkS.dxf
pcb_files/Pacifista_TinyFPGA/Pacifista_TinyFPGA-F_SilkS.dxf

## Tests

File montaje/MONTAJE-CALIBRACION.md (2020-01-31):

# PacifistaBot: Montaje y Calibración
PacifistaBot

El montaje y calibración del robot humanoide es relativamente sencillo y adecuado para la inicialización. Pero es necesario seguir unos pasos o unas indicaciones para simplificar el trabajo.

### Montaje

El montaje del robot está compuesto de dos partes, una mecánica y otra electrónica. Este trabajo se puede empezar por cualquiera de las dos partes para unirlas al finalizarlas. En el video que han realizado los de [OPRobots](https://twitter.com/OPRobots) al principio se puede ver el montaje mecánico y al final el montaje electrónico.

Botón de video de montaje (https://drive.google.com/file/d/10EezfLya-EukxTjCjV9P1Jr0ghWxqBgg)

También está documentado mediante twitter por [ionhs_FP](https://twitter.com/ionhs_FP) el proceso de montaje del robot humanoide:

- Parte [mecánica en twitter](https://twitter.com/ionhs_FP/status/1115969155814121472)
- Parte [electrónica en twitter](https://twitter.com/ionhs_FP/status/1116700309957509120)

### Ajuste y Calibración

Es importante tomarse el tiempo necesario para poder realizar el ajuste y la calibración lo mejor posible en el robot. Gracias a esto el uso será menos accidentado, habrá menos roturas y podremos tener el robot operativo una mayor cantidad de tiempo.

1. ##### Ajustes y holguras

   Durante el montaje hay 2 tipos de unioses, algunas son fijas y otras requieren cierta holgura para posibilitar el movimiento. Las que requieren holgura, hay que buscar el equilibrio para que por una parte las piezas estén bien posicionadas y por otra, no tengan una gran fricción durante el movimiento. Los codos y rodillas del robot como los de la foto, son los puntos donde hace falta un ajuste más fino.

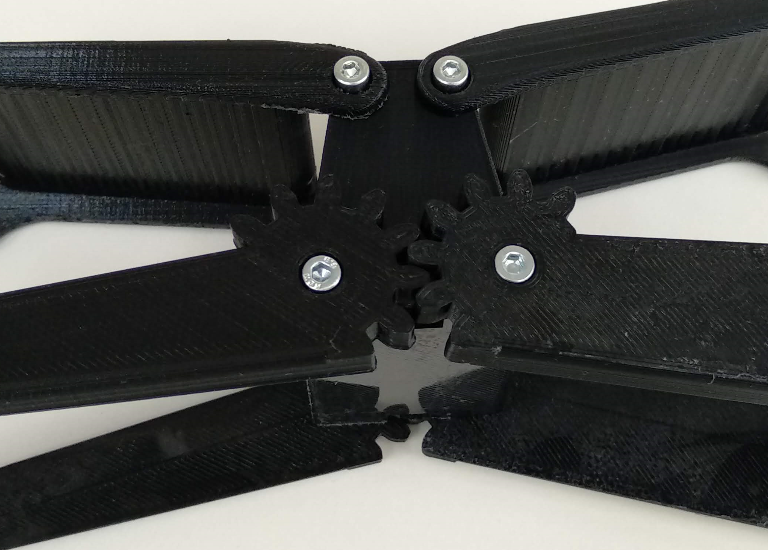
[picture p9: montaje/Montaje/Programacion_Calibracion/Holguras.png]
   

2. ##### Límites mecánicos

   Tras realizar el montaje se ha de comprobar a mano (sin meterle tensión) todos los movimientos del robot, comprobando que cada servomotor puede realizar los movimientos sin problemas. En el ejemplo de abajo se comprueba que el brazo puede realizar los 2 movimientos sin problemas: Poder plegarse contra el cuerpo y poder extenderse más que completamente.

   |                       Brazo recogido                       |                       Brazo extendido                       |
   | :--------------------------------------------------------: | :---------------------------------------------------------: |
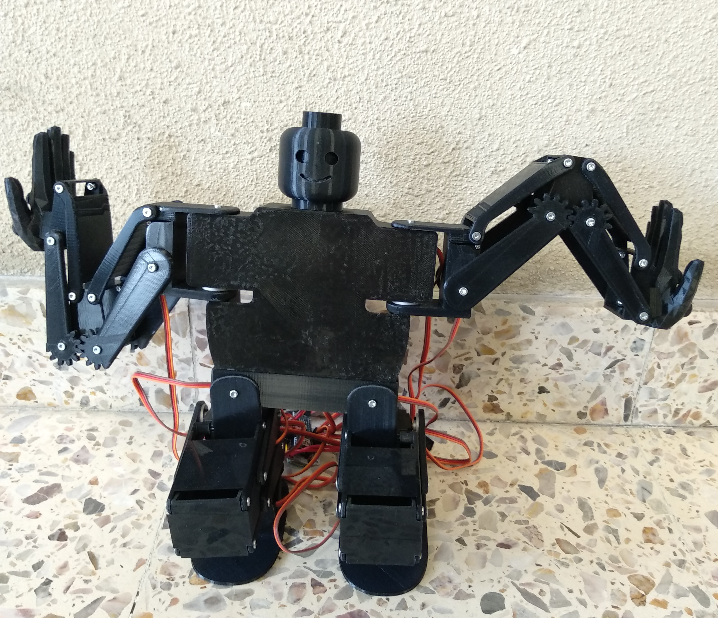
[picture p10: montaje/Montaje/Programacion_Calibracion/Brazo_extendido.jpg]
   |  |  |

   En el caso que algún servomotor no tuviera todo el recorrido mecánico, habría que desmontar la pieza impresa, mover el servomotor y volver a montar la pieza, hasta que tuviera todo el recorrido mecánico. En el caso de no realizarse este tipo de comprobaciones, es muy posible que al poco de empezar a usarse alguna pieza se rompa. En la imagen se puede ver la rotura de la pieza de plástico del codo del robot.

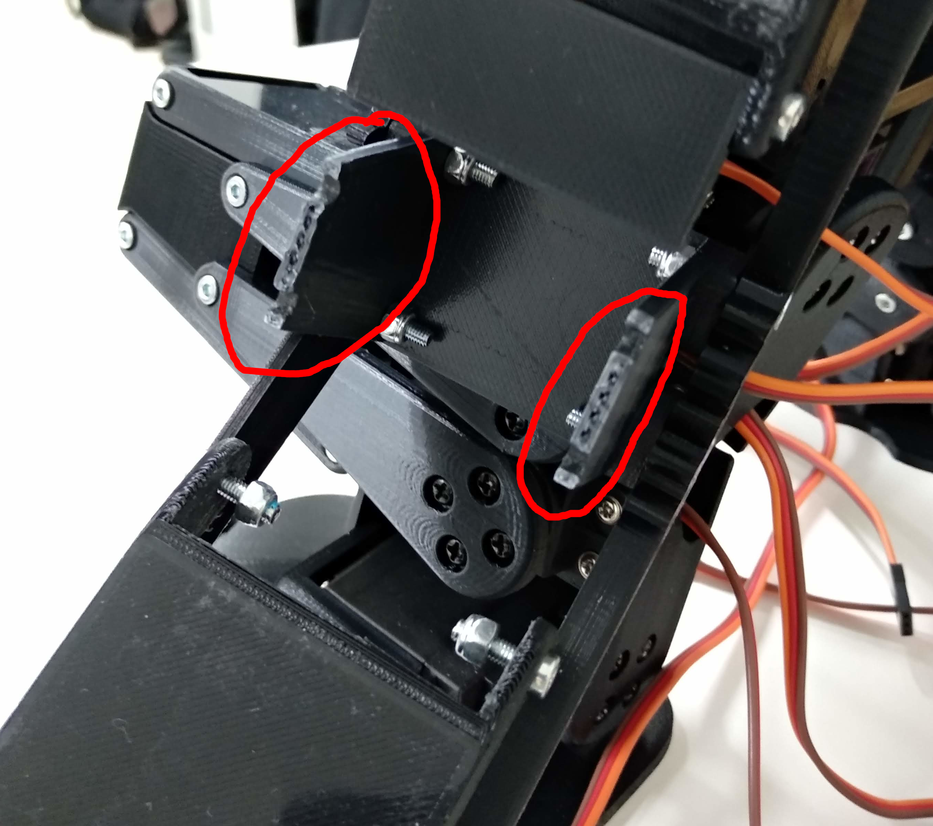
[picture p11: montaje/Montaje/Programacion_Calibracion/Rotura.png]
   

3. ##### Límites por software

   Una vez que se ha comprobado que mecánicamente está bien montado y con los límites ajustados, se ha de identificar los límites por software. Para ello se cargará un programa simple llamado [Configuración](./../source_code/Configuracion/Configuracion.ino), en el que se usará el pin A1 de la placa electrónica para conectar los servomotores y comunicarse por bluetooth:

   - Ordenador: [ScriptCommunicatorSerie](https://github.com/szieke/ScriptCommunicator_serial-terminal), [Putty](https://www.putty.org/)...
   - Android: [Bluetooth Electronics](https://www.keuwl.com/apps/bluetoothelectronics/)...

    De esta manera se irá viendo  la posición del servomotor por serie y desde el PC o móvil se podrá desplazar grado a grado la posición. Para conocer el ángulo límite del robot se ha de ir sustituyendo en el pin A1 uno a uno todos los servomotores del robot.

   |           Placa alimentada con conexión al pin A1            |               Captura de la pantalla del movil               |
   | :----------------------------------------------------------: | :----------------------------------------------------------: |
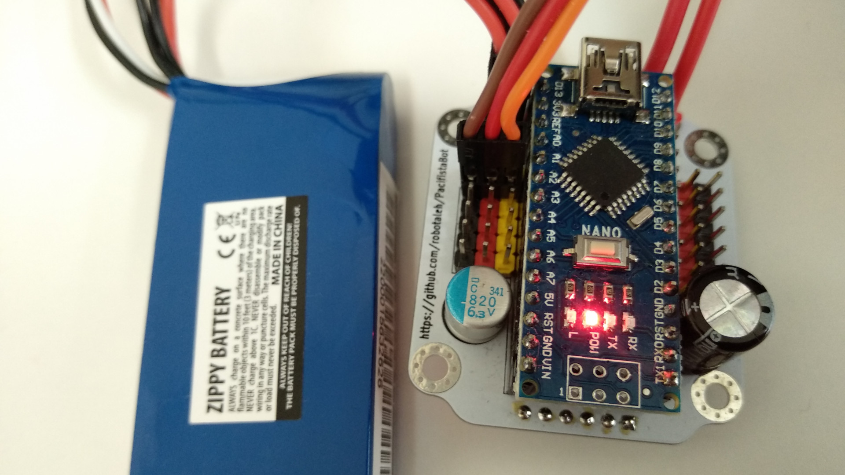
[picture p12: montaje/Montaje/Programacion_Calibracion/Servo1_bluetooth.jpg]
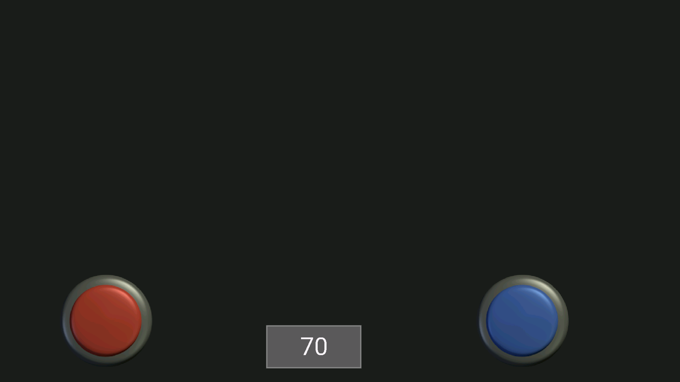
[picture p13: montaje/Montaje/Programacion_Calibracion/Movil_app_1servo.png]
   |  |  |

   En las imágenes de arriba se muestra el servomotor del hombro derecho del robot conectado a la placa en el pin A1. También la imagen del la aplicación del móvil ([Descargar panel](../source_code/BluetoothElectronics/Bluetooth_Electronics_Panels_0003.kwl) de BluetoothElectronics) donde se ve que el servomotor está a 70º y mediante los 2 botones se puede desplazar el servomotor hacia arriba o abajo. Esta información (los límites de cada servomotor) hay que ir consiguiéndola de cada uno de los servomotores del robot.

4. ##### Tecnología y Diagrama de Bloques

   Mediante el siguiente diagrama de bloques se puede ver los bloques tecnológicos y las relaciones que hay entre ellos en el robot humanoide.

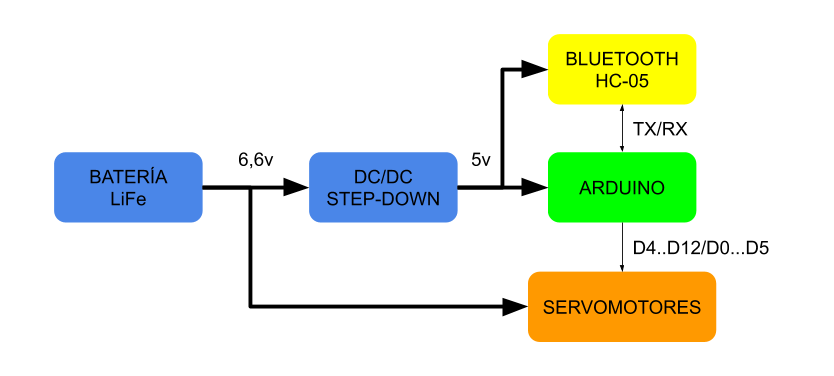
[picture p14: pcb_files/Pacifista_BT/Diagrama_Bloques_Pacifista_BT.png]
   

   Los archivos originales del [diagrama de bloques](../pcb_files/Pacifista_BT/Diagrama_Bloques_Pacifista_BT.svg) han sido creados en Inkscape en el formato SVG.

5. ##### Conexión de los Servomotores

   Para poder mover el robot en su conjunto es imprescindible conectar todos los servomotores a la placa controladora.

   | Pinout del Robot                                        | Pin out de la PCB                                          |
   | ------------------------------------------------------- | ---------------------------------------------------------- |
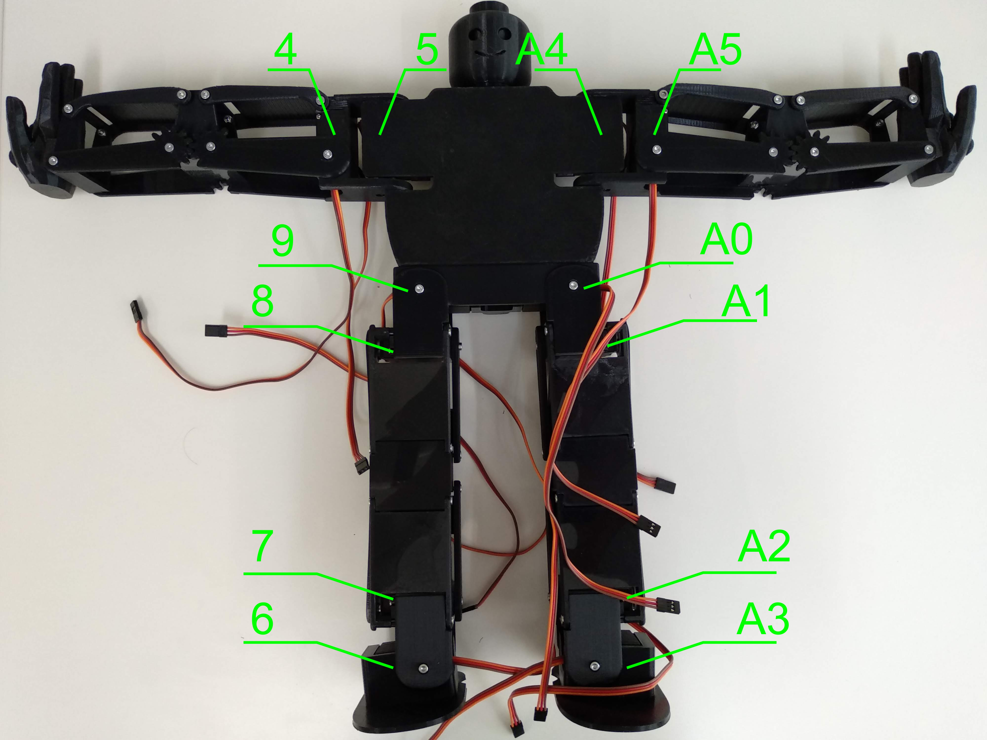
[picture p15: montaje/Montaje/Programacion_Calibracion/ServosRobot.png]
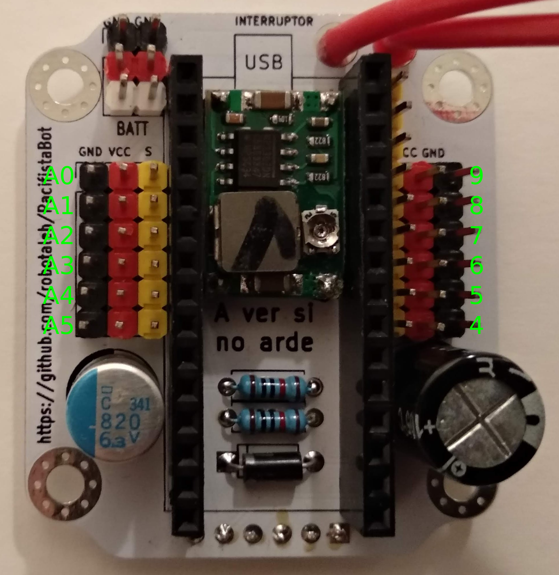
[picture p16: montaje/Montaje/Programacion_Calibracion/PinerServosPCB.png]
   |  |  |

   Los archivos originales del [PinoutRobot](./Montaje/Programacion_Calibracion/RobotPosicionServo.svg) así como el del [PinoutPCB](./Montaje/Programacion_Calibracion/PCBnumeracionServos.svg) han sido creados en Inkscape en el formato SVG.

6. ##### Cargar programa principal

   El programa principal necesita que se tengan cargadas 3 librerias (Octosnake, Wire y Servo) en el IDE de Arduino. El [programa principal](./../source_code/Programa_Principal_OPRobots/) está estructurado en 5 pestañas (Main, Comunicaciones, Init, Movimientos y Servocontrol) que se cargarán al abrir el archivo Main. Una vez abierto hay que ir a la pestaña Init para definir las posiciones de los 12 servos, que hemos obtenido en el punto **3 Limites por servo**. Hay que tener en cuenta que en la posición de init el robot ha de estar depie (las piernas extendidas) y con los brazos recogidos, por lo que los límites que pongamos serán para obtener esa posición.

   Tras definir la posición inicial hay que ir a la pestaña Movimientos y a la función posicion_hombros y en el switch/Case definir la posición de los hombros adelante y atras. En caso de no hacerlo la función hombro no funciona correctamente y además no se puede volver a poner los hombros en su posición central.

   Otro de los movimientos que hay que ajustar es el de agachado. En la pestaña Movimientos y en la función posicion_agachado hay 8 arrays donde se establece como han de estar 8 servomotores al finalizar la posición de agachado. Estas 8 posiciones conviene ajustarlas a nuestras necesidades para que el robot flexe correctamente las rodillas y quede agachado.

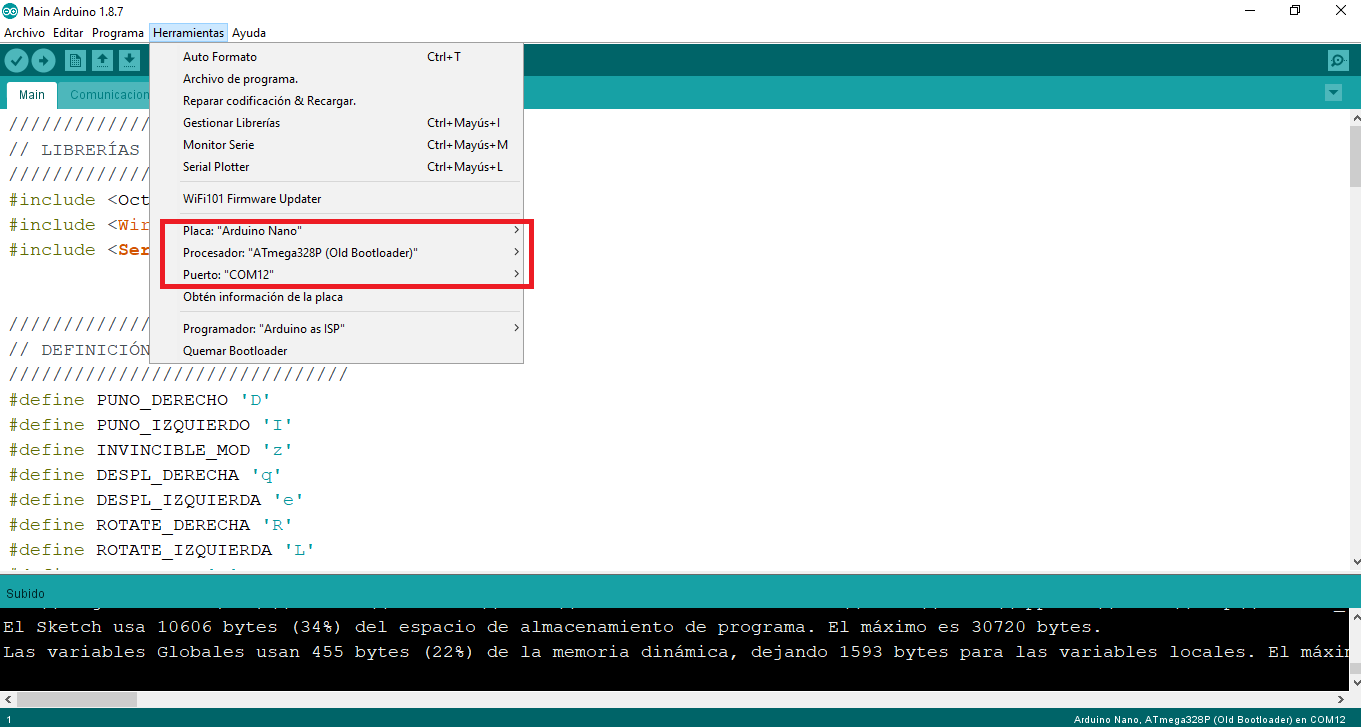
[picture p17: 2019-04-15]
montaje/Montaje/Programacion_Calibracion/ArduinoIDEconfiguracion.png

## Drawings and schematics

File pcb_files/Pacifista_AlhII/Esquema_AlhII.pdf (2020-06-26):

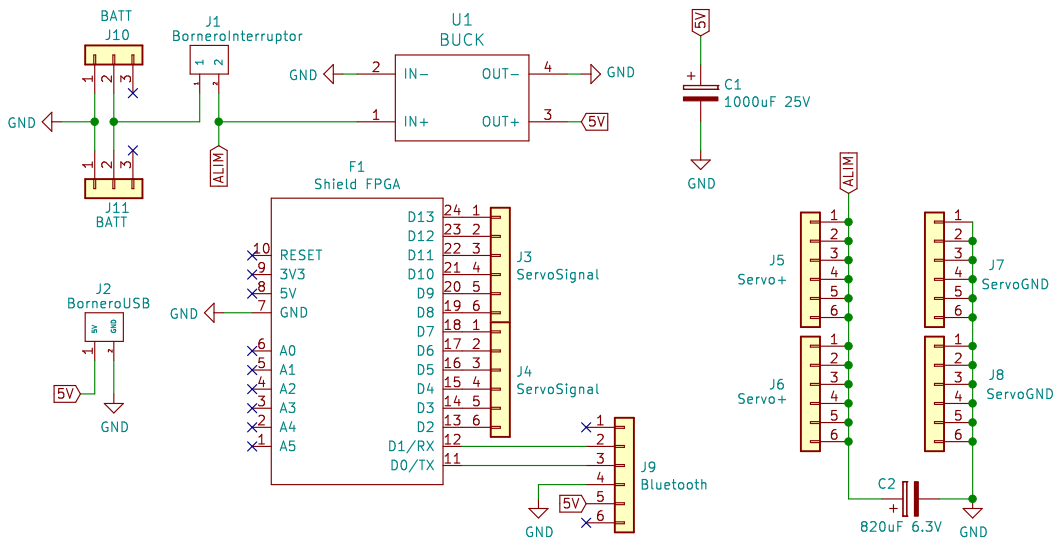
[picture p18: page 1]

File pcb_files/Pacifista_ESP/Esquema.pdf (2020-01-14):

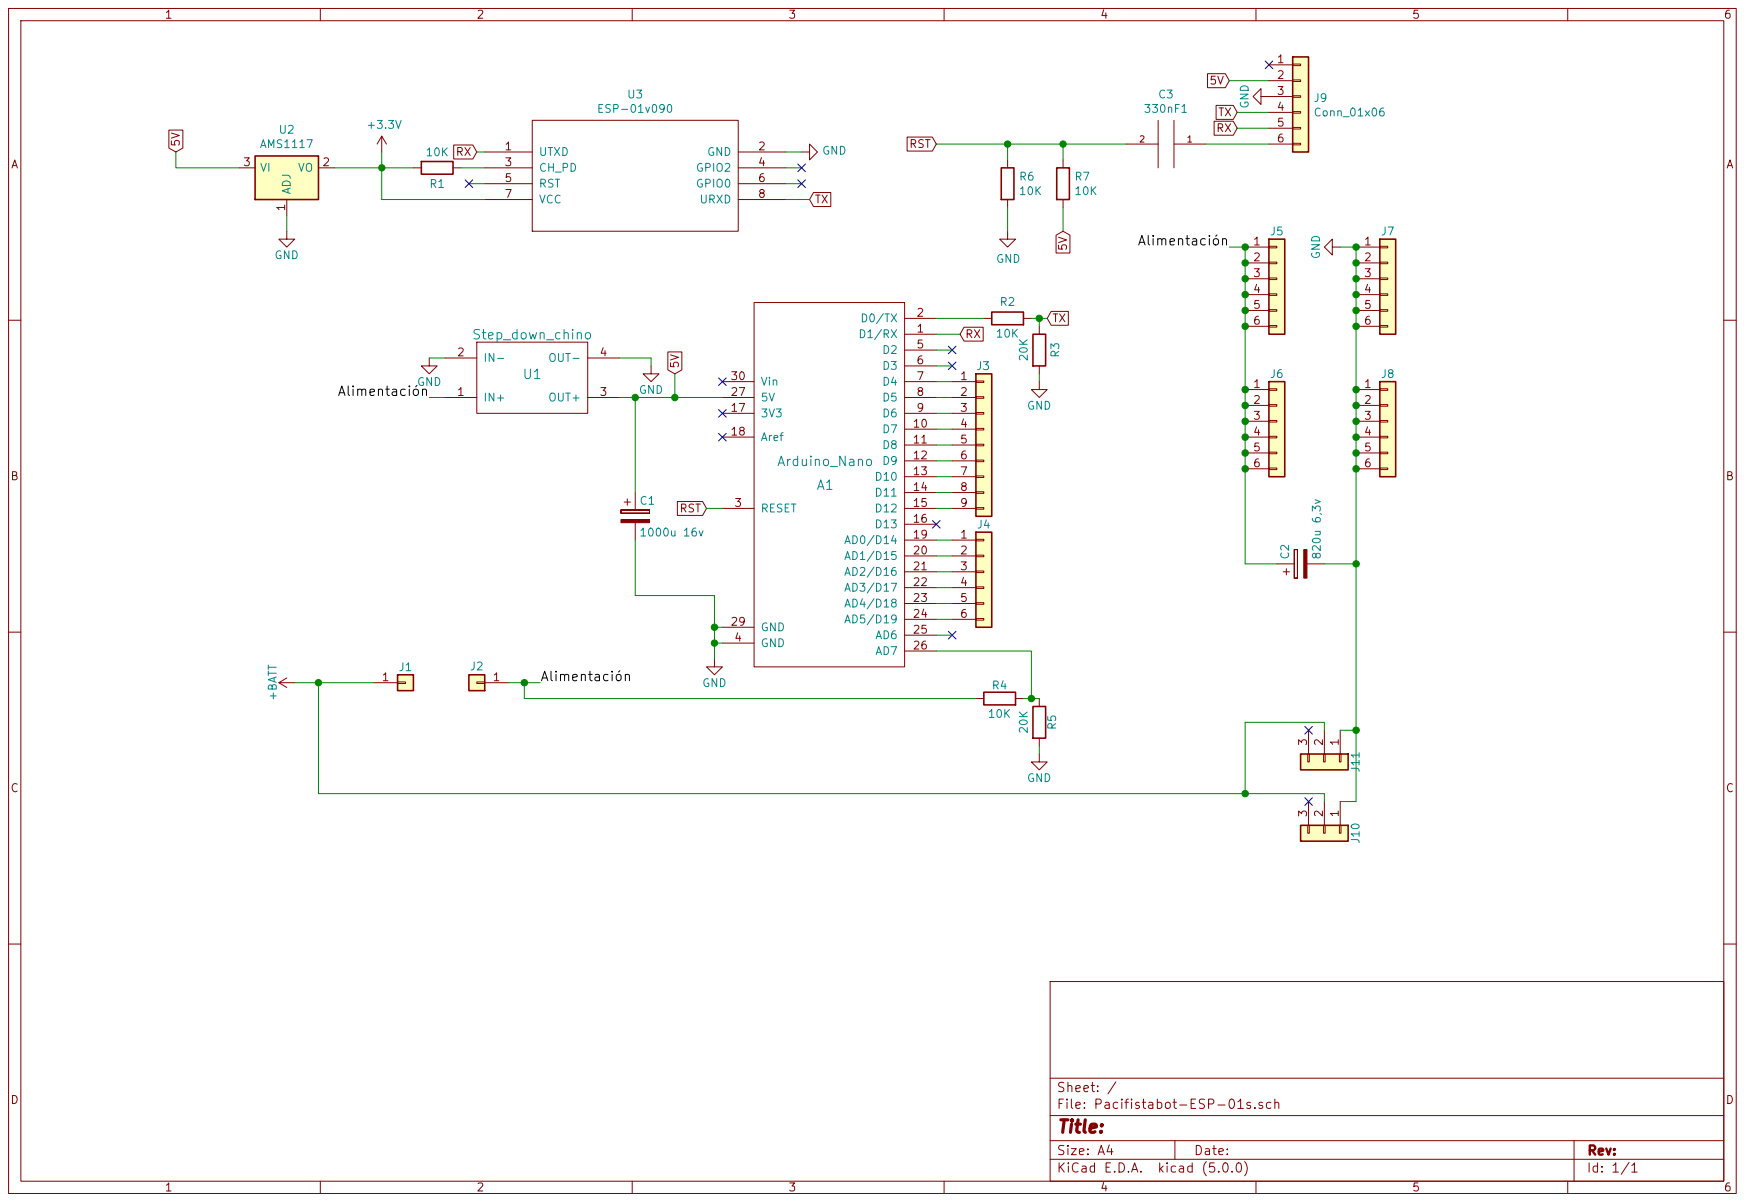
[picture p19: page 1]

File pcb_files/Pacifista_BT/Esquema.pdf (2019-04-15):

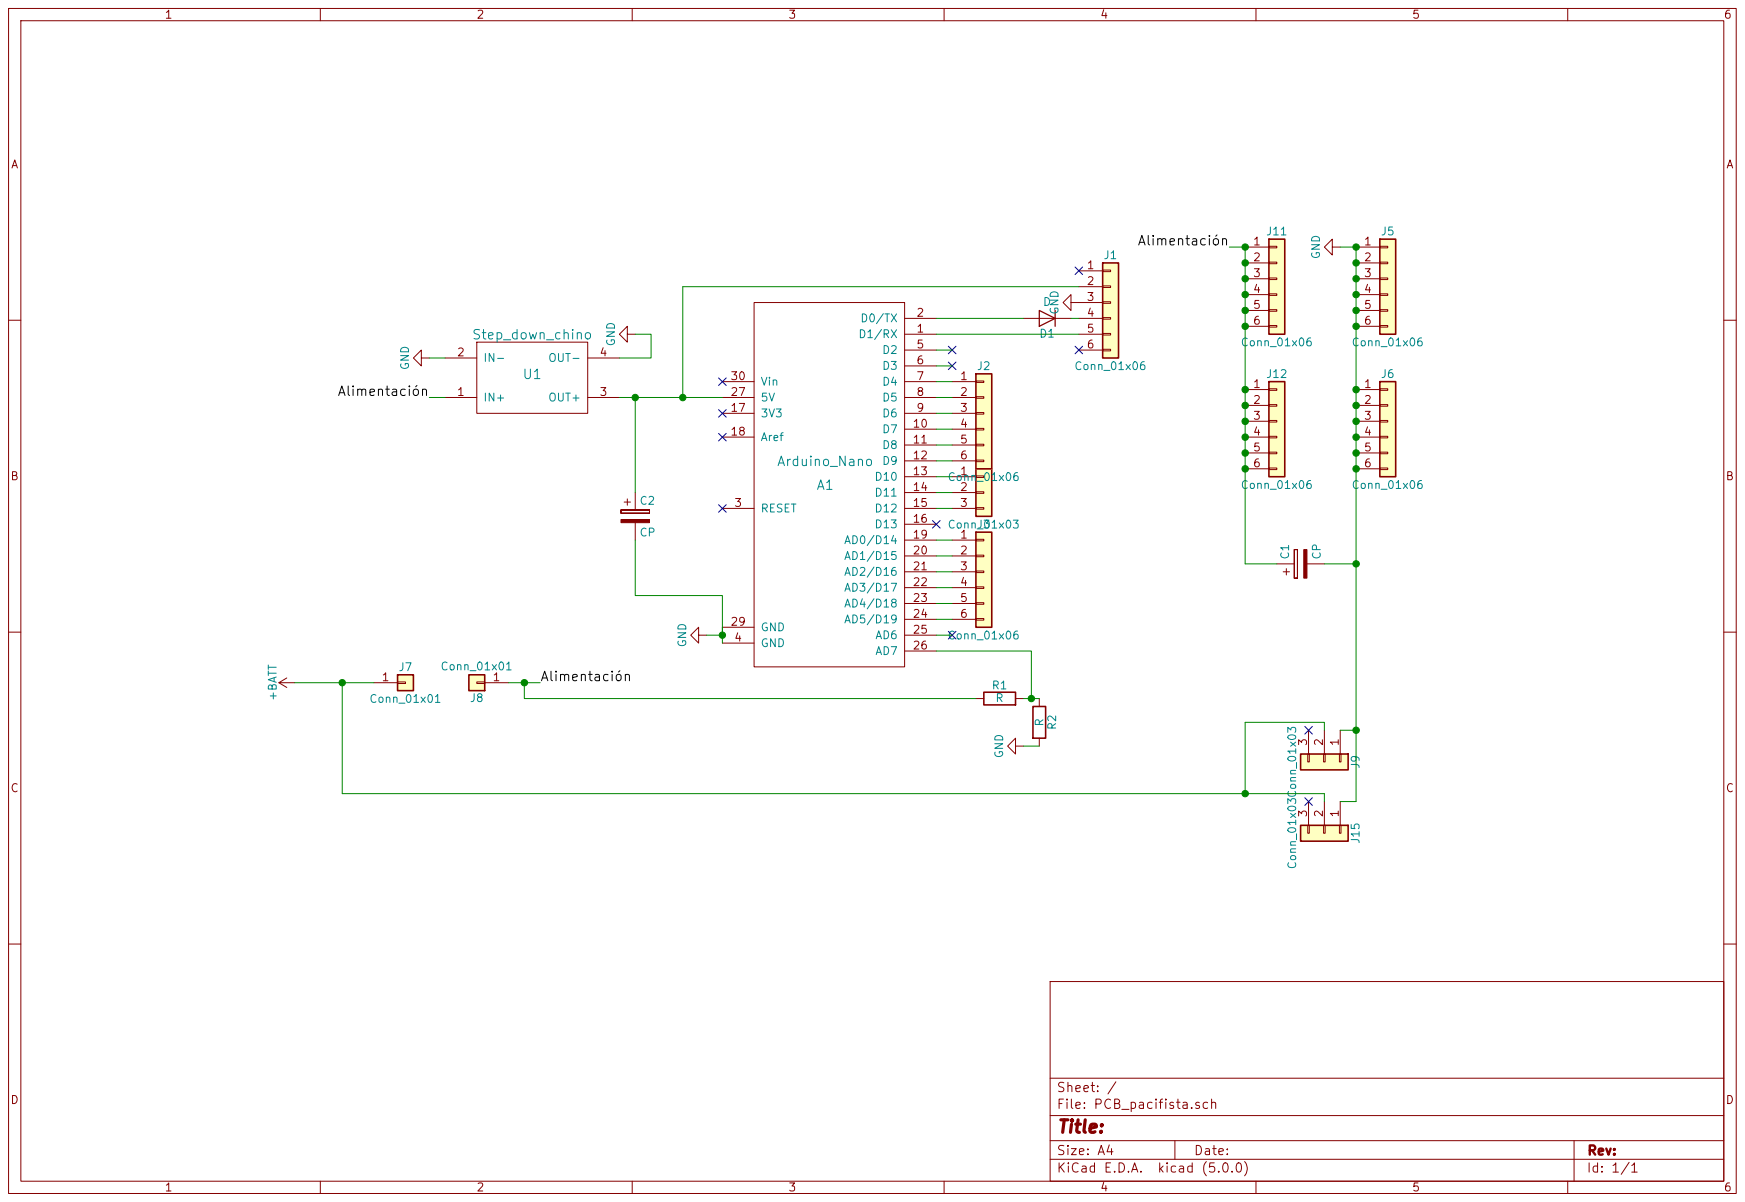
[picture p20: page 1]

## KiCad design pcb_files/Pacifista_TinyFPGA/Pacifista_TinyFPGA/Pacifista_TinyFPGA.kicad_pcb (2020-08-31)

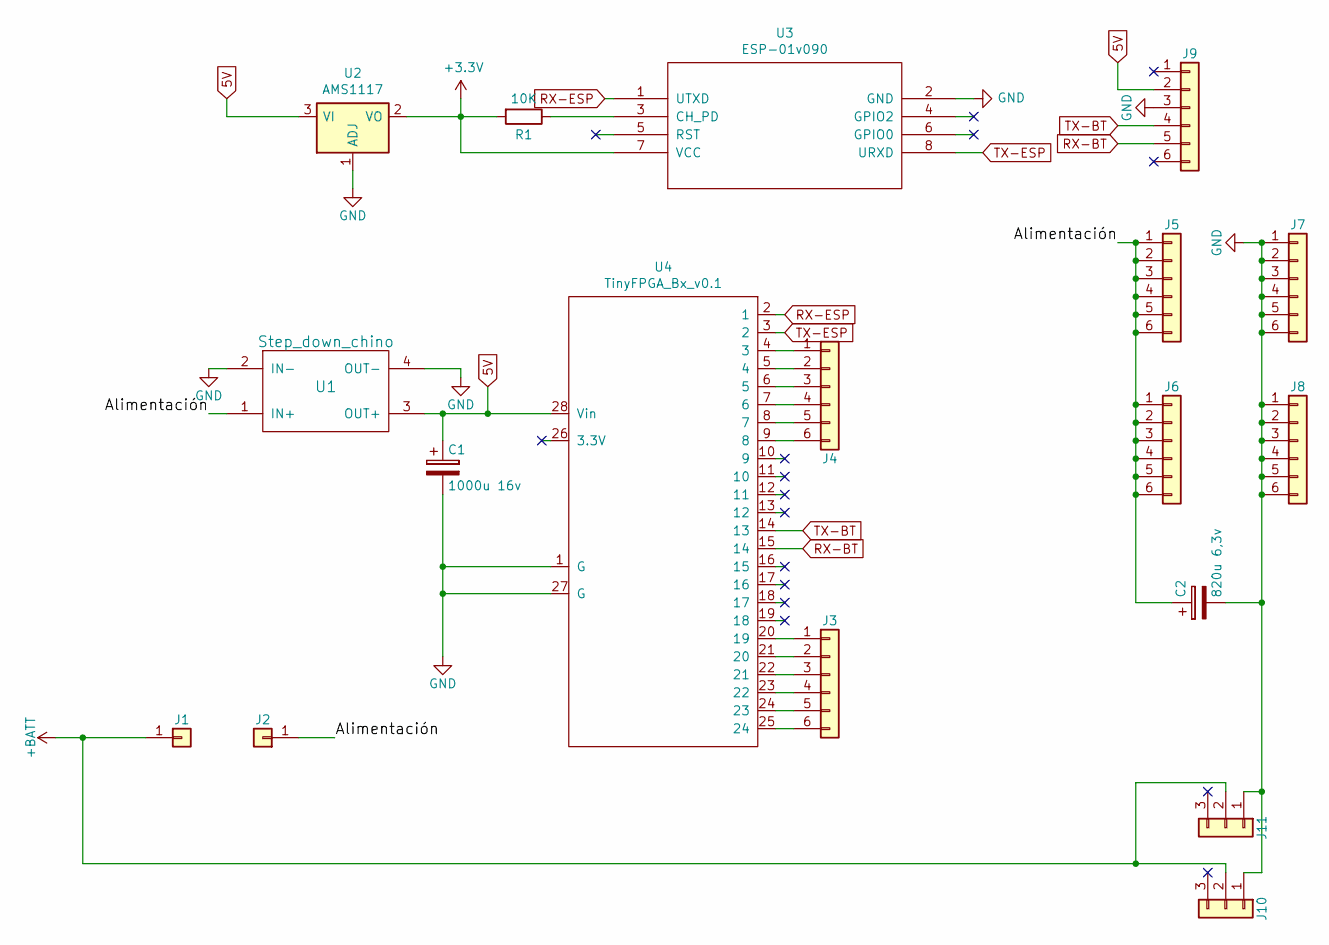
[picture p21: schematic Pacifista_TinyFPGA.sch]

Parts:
C1: 1000u 16v; CP_Radial_D8.0mm_P3.80mm
C2: 820u 6,3v; CP_Radial_D10.0mm_P5.00mm
J1, J2: Conn_01x01; SolderWirePad_single_1-5mmDrill
J3: Conn_01x06; PinSocket_1x06_P2.54mm_Vertical
J4, J5, J6, J7, J8: Conn_01x06; Pin_Header_Straight_1x06_Pitch2.54mm
J9: Bluetooth hc_05; Pin_Header_Straight_1x06_Pitch2.54mm
J10, J11: Conn_01x03; Pin_Header_Straight_1x03_Pitch2.54mm
R1: 10K; R_1206_3216Metric_Pad1.42x1.75mm_HandSolder
U1: Step_down_chino
U2: AMS1117; SOT-223-3_TabPin2
U3: ESP-01v090; PinHeader_2x04_P2.54mm_Vertical
U4: TinyFPGA_Bx_v0.1

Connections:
5V: C1.1, J9.2, U1.3 (OUT+), U2.3 (VI), U4.28 (Vin)
+3V3: R1.2, U2.2 (VO), U3.7 (VCC)
+BATT: J1.1, J10.2, J11.2
/Alimentación: C2.1, J2.1, J5.1, J5.2, J5.3, J5.4, J5.5, J5.6, J6.1, J6.2, J6.3, J6.4, J6.5, J6.6, U1.1 (IN+)
GND: C1.2, C2.2, J7.1, J7.2, J7.3, J7.4, J7.5, J7.6, J8.1, J8.2, J8.3, J8.4, J8.5, J8.6, J9.3, J10.1, J11.1, U1.2 (IN-), U1.4 (OUT-), U2.1 (ADJ), U3.2 (GND), U4.1 (G), U4.27 (G)
unnamed: J3.1, U4.20 (19)
unnamed: J3.2, U4.21 (20)
unnamed: J3.3, U4.22 (21)
unnamed: J3.4, U4.23 (22)
unnamed: J3.5, U4.24 (23)
unnamed: J3.6, U4.25 (24)
unnamed: J4.1, U4.4 (3)
unnamed: J4.2, U4.5 (4)
unnamed: J4.3, U4.6 (5)
unnamed: J4.4, U4.7 (6)
unnamed: J4.5, U4.8 (7)
unnamed: J4.6, U4.9 (8)
unnamed: R1.1, U3.3 (CH_PD)
RX-BT: J9.5, U4.15 (14)
RX-ESP: U3.1 (UTXD), U4.2 (1)
TX-BT: J9.4, U4.14 (13)
TX-ESP: U3.8 (URXD), U4.3 (2)

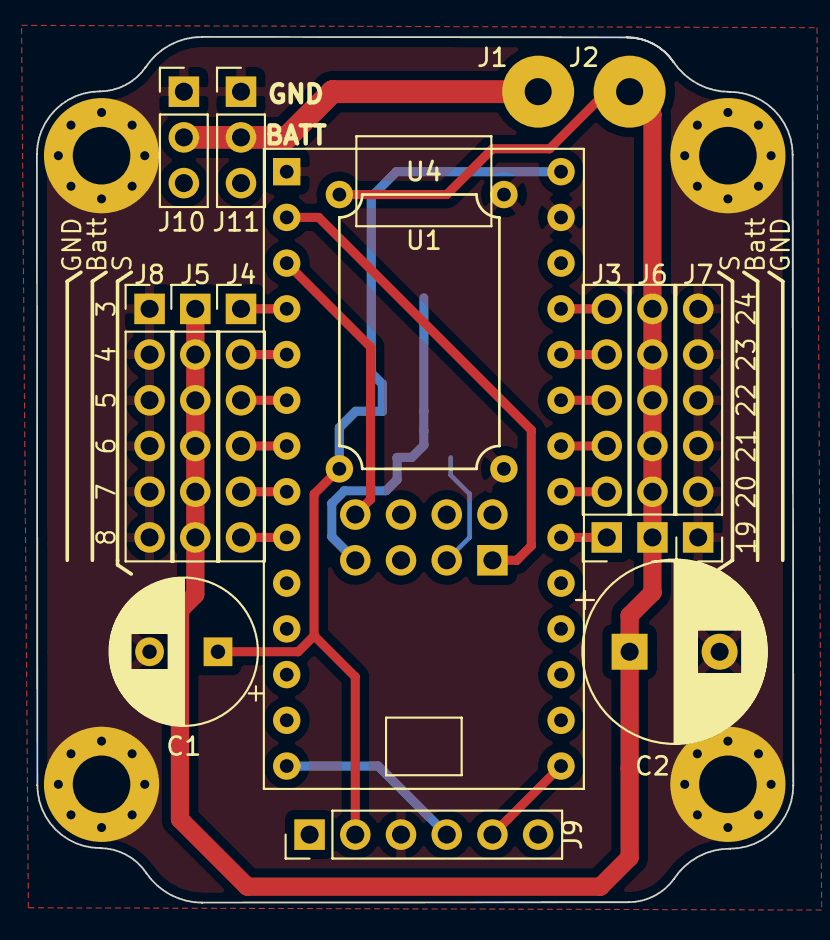
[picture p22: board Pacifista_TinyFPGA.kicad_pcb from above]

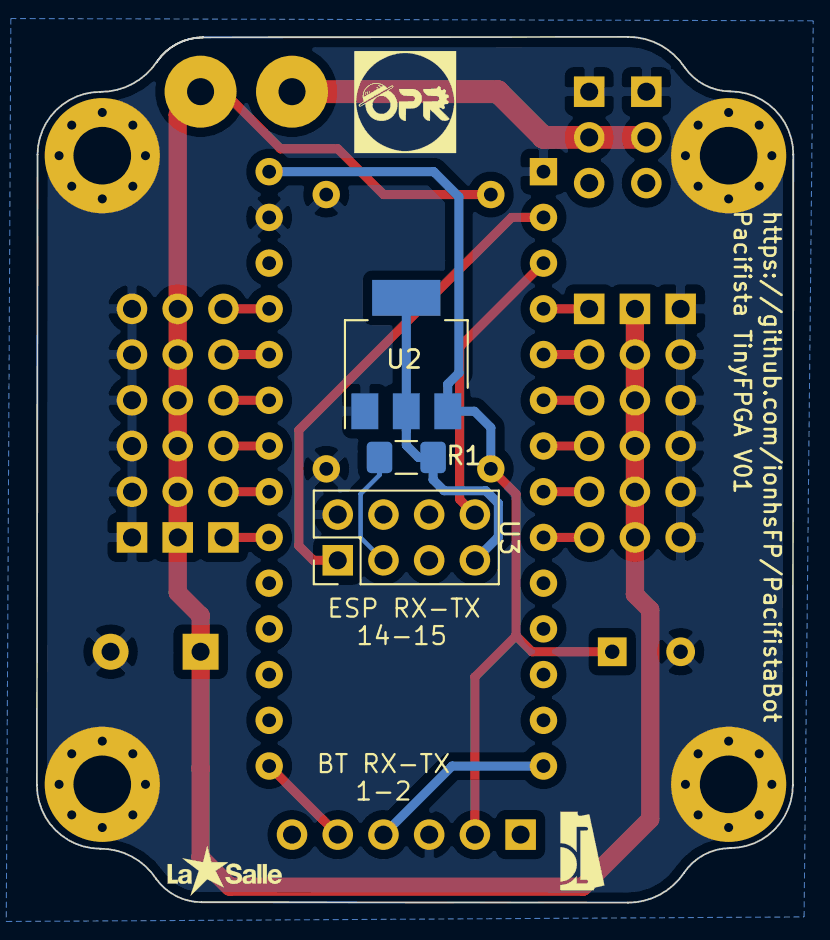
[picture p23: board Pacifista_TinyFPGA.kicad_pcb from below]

Board: 2 copper layers, 42.0 x 48.1 mm, 18 parts (3 on the bottom side), 22 nets.

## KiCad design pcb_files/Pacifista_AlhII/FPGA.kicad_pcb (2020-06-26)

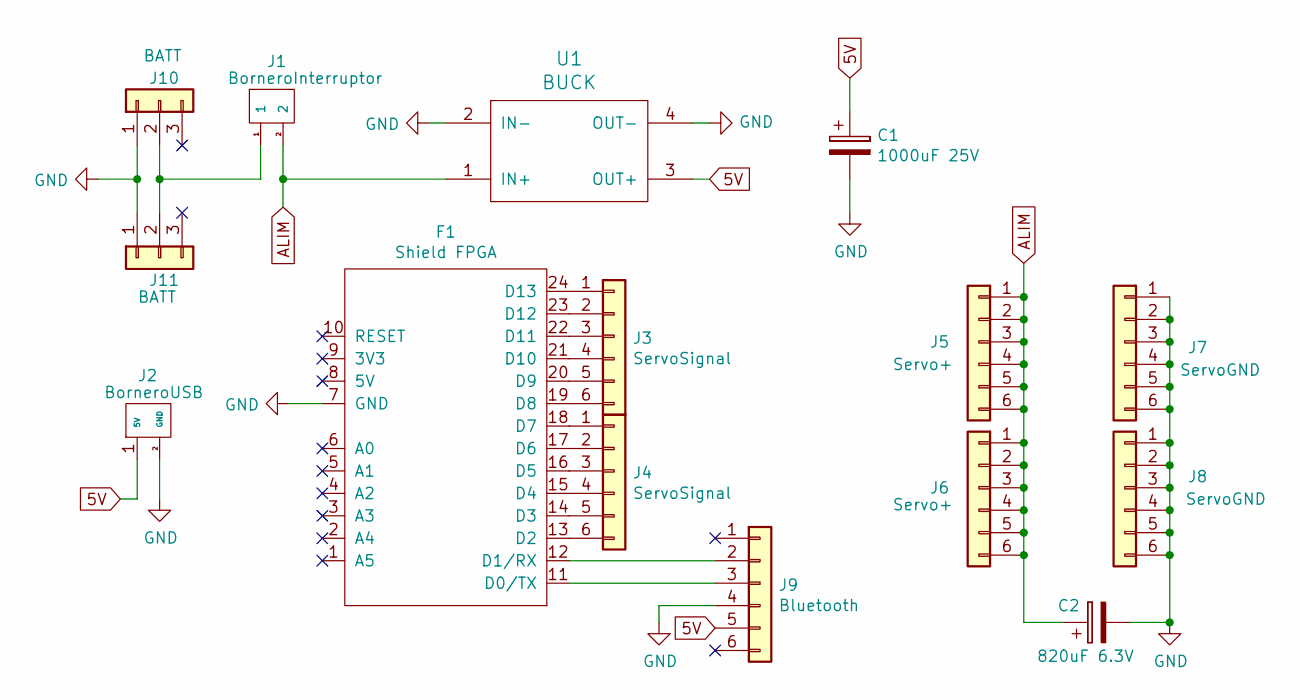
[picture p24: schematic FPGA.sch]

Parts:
C1: 1000uF 25V; CP_Radial_D10.0mm_P3.80mm
C2: 820uF 6.3V; CP_Radial_D8.0mm_P3.50mm
F1: Shield FPGA; Shield
J1: BorneroInterruptor; Bornero Interruptor
J2: BorneroUSB; Bornero USB
J3, J4: ServoSignal; Header1x06
J5, J6: Servo+; Header1x06
J7, J8: ServoGND; Header1x06
J9: Bluetooth; Header1x06
J10, J11: BATT; Header1x03
U1: BUCK

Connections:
5V: C1.1, J2.1 (5V), J9.5, U1.3 (OUT+)
ALIM: C2.1, J1.2, J5.1, J5.2, J5.3, J5.4, J5.5, J5.6, J6.1, J6.2, J6.3, J6.4, J6.5, J6.6, U1.1 (IN+)
GND: C1.2, C2.2, F1.7 (GND), J2.2 (GND), J7.1, J7.2, J7.3, J7.4, J7.5, J7.6, J8.1, J8.2, J8.3, J8.4, J8.5, J8.6, J9.4, J10.1, J11.1, U1.2 (IN-), U1.4 (OUT-)
unnamed: F1.11 (D0/TX), J9.3
unnamed: F1.12 (D1/RX), J9.2
unnamed: F1.13 (D2), J4.6
unnamed: F1.14 (D3), J4.5
unnamed: F1.15 (D4), J4.4
unnamed: F1.16 (D5), J4.3
unnamed: F1.17 (D6), J4.2
unnamed: F1.18 (D7), J4.1
unnamed: F1.19 (D8), J3.6
unnamed: F1.20 (D9), J3.5
unnamed: F1.21 (D10), J3.4
unnamed: F1.22 (D11), J3.3
unnamed: F1.23 (D12), J3.2
unnamed: F1.24 (D13), J3.1
unnamed: J1.1, J10.2, J11.2

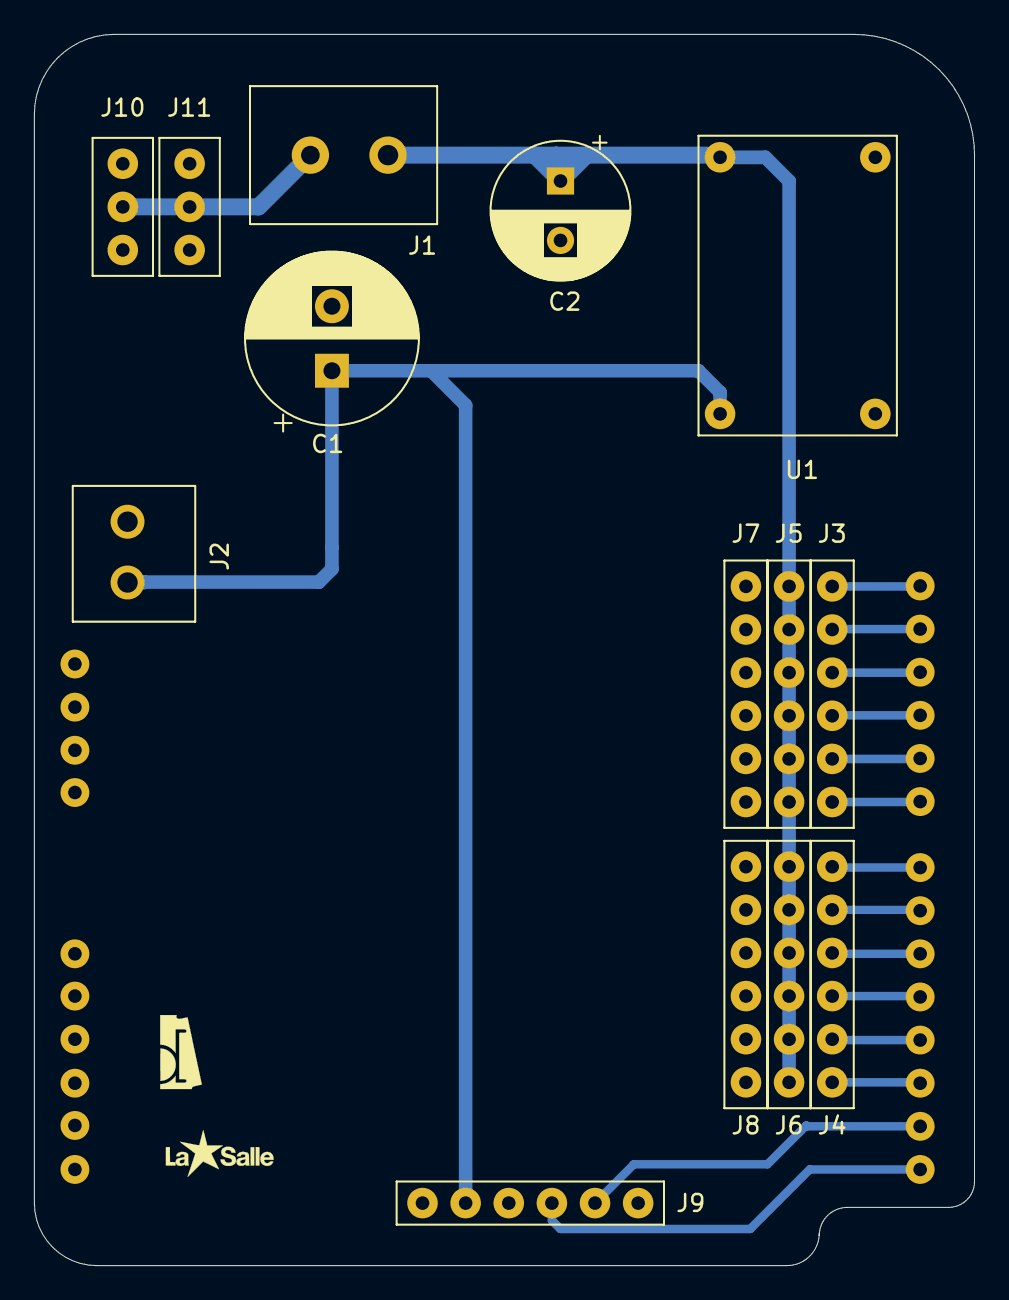
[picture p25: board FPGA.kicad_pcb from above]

Board: 2 copper layers, 55.4 x 72.5 mm, 15 parts (0 on the bottom side), 18 nets.

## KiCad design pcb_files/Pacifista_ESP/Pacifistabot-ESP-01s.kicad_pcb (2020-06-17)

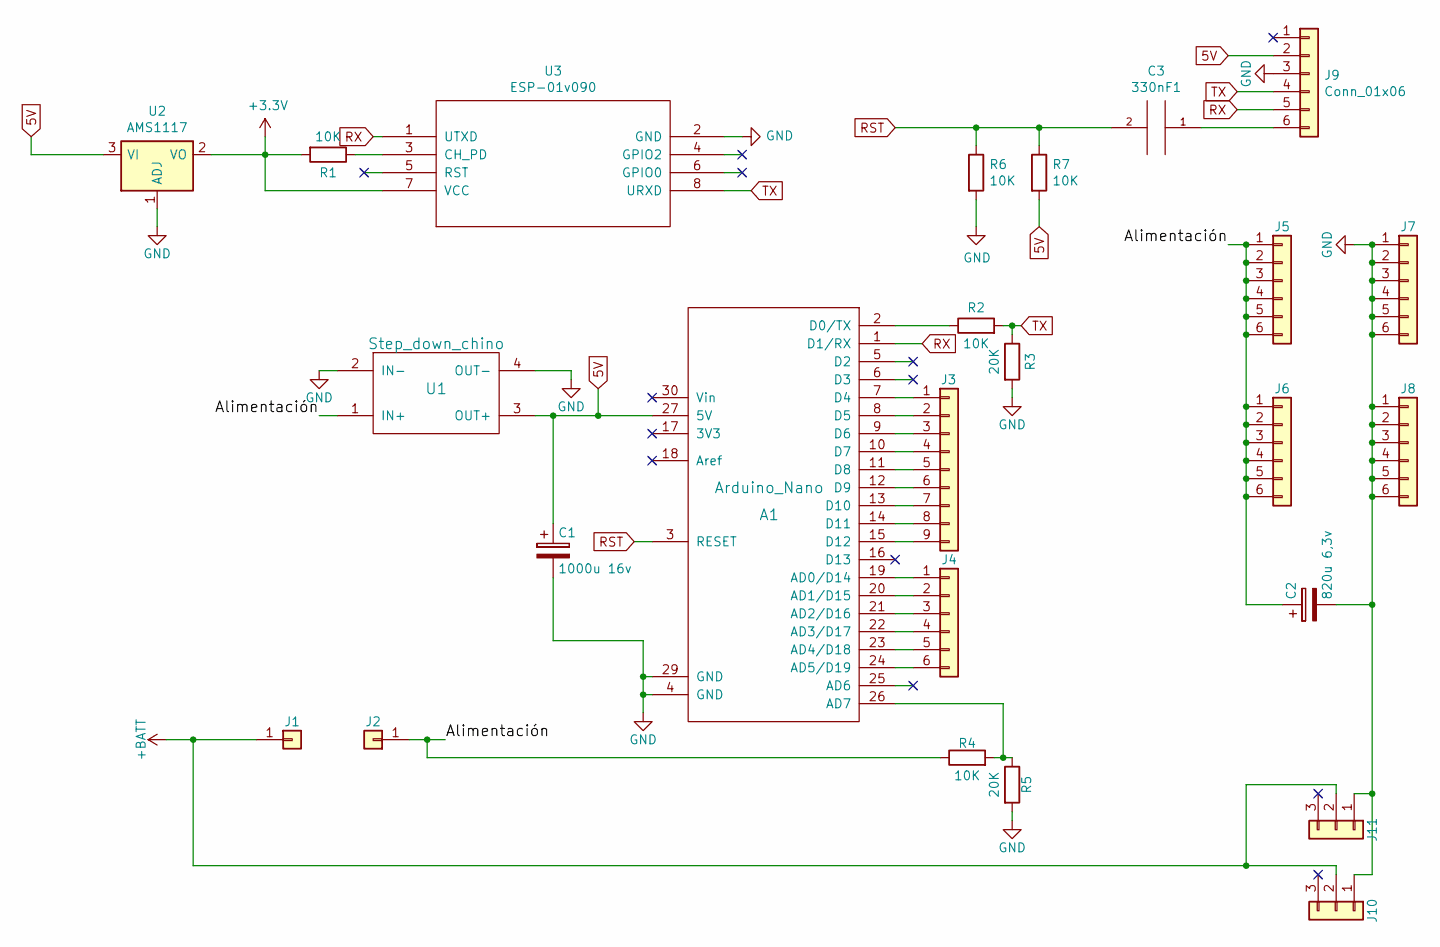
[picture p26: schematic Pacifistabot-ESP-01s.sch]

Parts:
A1: Arduino_Nano; arduino_nano
C1: 1000u 16v; CP_Radial_D8.0mm_P3.80mm
C2: 820u 6,3v; CP_Radial_D10.0mm_P5.00mm
C3: 330nF1; C_1206_3216Metric_Pad1.42x1.75mm_HandSolder
J1, J2: Conn_01x01; SolderWirePad_single_1-5mmDrill
J3: Conn_01x09; PinHeader_1x09_P2.54mm_Vertical
J4, J5, J6, J7, J8: Conn_01x06; Pin_Header_Straight_1x06_Pitch2.54mm
J9: Conn_01x06; PinSocket_1x06_P2.54mm_Vertical
J10, J11: Conn_01x03; Pin_Header_Straight_1x03_Pitch2.54mm
R1, R6, R7: 10K; R_1206_3216Metric_Pad1.42x1.75mm_HandSolder
R2, R4: 10K; R_Axial_DIN0207_L6.3mm_D2.5mm_P7.62mm_Horizontal
R3, R5: 20K; R_Axial_DIN0207_L6.3mm_D2.5mm_P7.62mm_Horizontal
U1: Step_down_chino
U2: AMS1117; SOT-223-3_TabPin2
U3: ESP-01v090; PinHeader_2x04_P2.54mm_Vertical

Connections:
5V: A1.27 (5V), C1.1, J9.2, R7.2, U1.3 (OUT+), U2.3 (VI)
+3V3: R1.2, U2.2 (VO), U3.7 (VCC)
+BATT: J1.1, J10.2, J11.2
/Alimentación: C2.1, J2.1, J5.1, J5.2, J5.3, J5.4, J5.5, J5.6, J6.1, J6.2, J6.3, J6.4, J6.5, J6.6, R4.1, U1.1 (IN+)
GND: A1.4 (GND), A1.29 (GND), C1.2, C2.2, J7.1, J7.2, J7.3, J7.4, J7.5, J7.6, J8.1, J8.2, J8.3, J8.4, J8.5, J8.6, J9.3, J10.1, J11.1, R3.2, R5.2, R6.2, U1.2 (IN-), U1.4 (OUT-), U2.1 (ADJ), U3.2 (GND)
unnamed: A1.2 (D0/TX), R2.1
unnamed: A1.7 (D4), J3.1
unnamed: A1.8 (D5), J3.2
unnamed: A1.9 (D6), J3.3
unnamed: A1.10 (D7), J3.4
unnamed: A1.11 (D8), J3.5
unnamed: A1.12 (D9), J3.6
unnamed: A1.13 (D10), J3.7
unnamed: A1.14 (D11), J3.8
unnamed: A1.15 (D12), J3.9
unnamed: A1.19 (AD0/D14), J4.1
unnamed: A1.20 (AD1/D15), J4.2
unnamed: A1.21 (AD2/D16), J4.3
unnamed: A1.22 (AD3/D17), J4.4
unnamed: A1.23 (AD4/D18), J4.5
unnamed: A1.24 (AD5/D19), J4.6
unnamed: A1.26 (AD7), R4.2, R5.1
unnamed: C3.1, J9.6
unnamed: R1.1, U3.3 (CH_PD)
RST: A1.3 (RESET), C3.2, R6.1, R7.1
RX: A1.1 (D1/RX), J9.5, U3.1 (UTXD)
TX: J9.4, R2.2, R3.1, U3.8 (URXD)

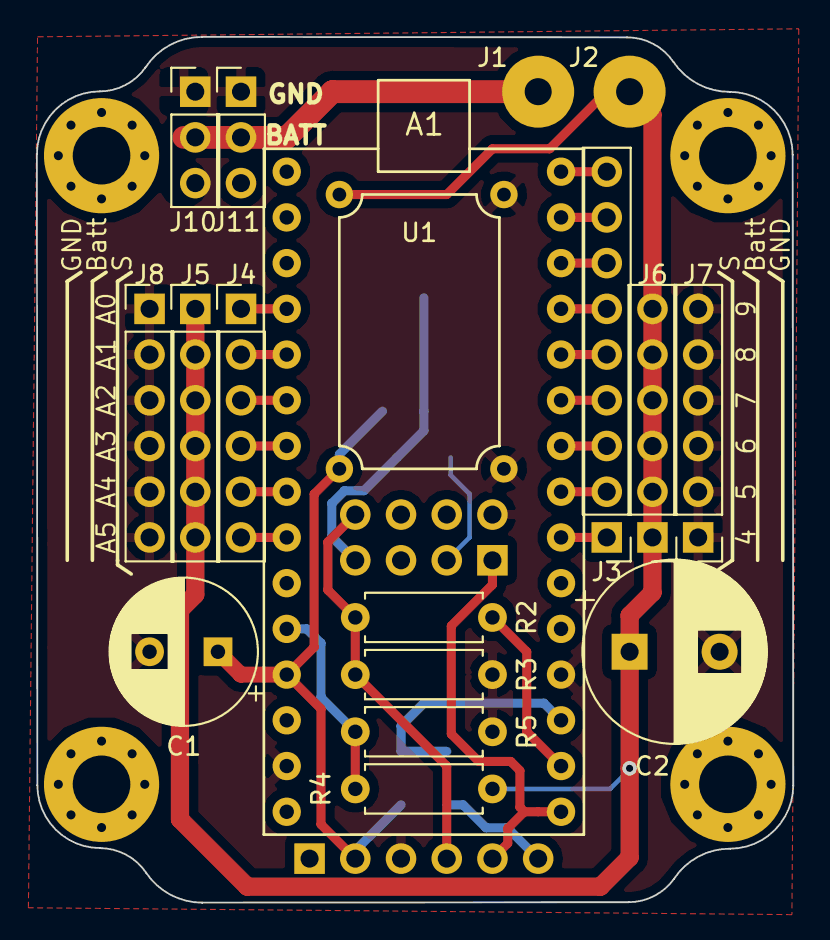
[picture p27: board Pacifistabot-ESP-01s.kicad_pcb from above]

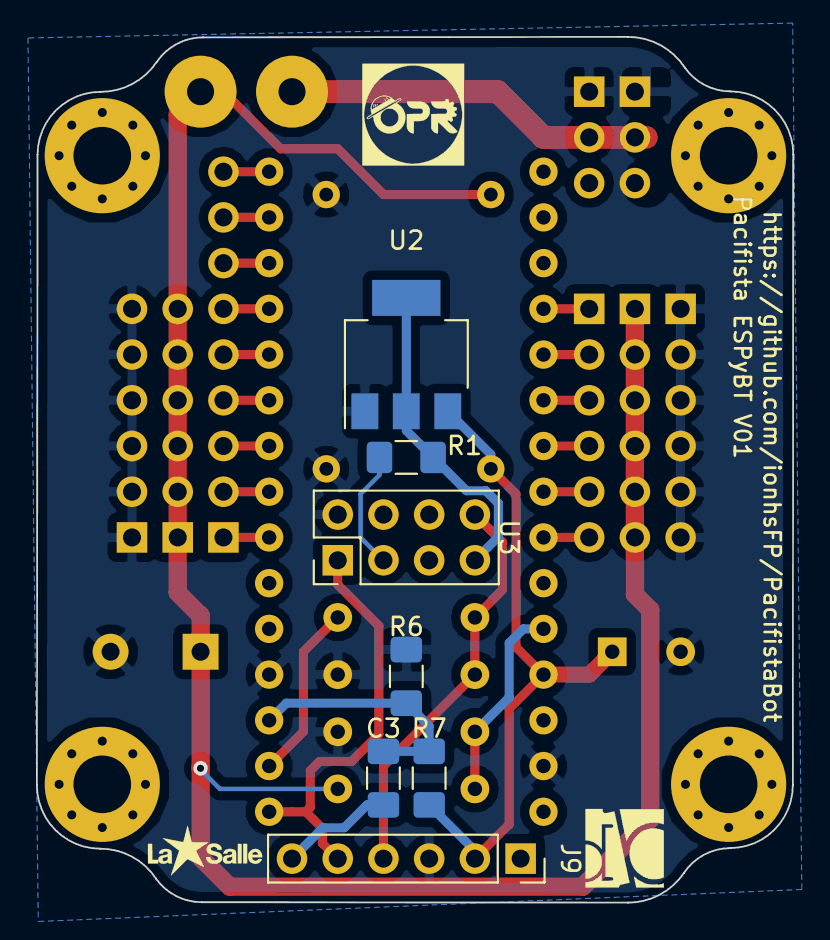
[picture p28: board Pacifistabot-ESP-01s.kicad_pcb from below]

Board: 2 copper layers, 42.0 x 48.1 mm, 25 parts (7 on the bottom side), 27 nets.

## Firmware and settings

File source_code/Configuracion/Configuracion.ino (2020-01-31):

/*

Konfigurazioa_V1.ino

Este programa sirve para buscar lo límites de los servomoteres del robot humanoide PacifistaBot.
De esta manera se evitarán roturas de las articulaciones del robot.

Para poder configurar los límites del servomotor, se conectará cada uno de los servos de uno en uno
y partiendo el servomotor de la posición 90º, se enviará por serie los caracteres "a" o "b".
Esto hará que el valor de la posición se incremente o decremente por lo que, el usuario tendrá que
ir apuntando el valor límite de cada uno de los 12 servos del robot. Ejemplo de los valores logrados:

Hombro derecho (Atras/Medio/Adelante): 140/68/0
Brazo derecho (Extendido/Plexado): 168/113

Hombro izquierdo (Atras/Medio/Adelante): 33/84/161
Brazo izquierdo (Extendido/Plexado): 28/92

Cadera derecho (Exterior/Medio): 145/85
Rodilla derecho (Extendido/Plexado): 84/151
Tobillo derecho (Extendido/Plexado): 113/34
Pie derecho (Exterior/Apoyo/Interior): 72/89/160


Cadera izquierdo (Exterior/Medio): 20/69
Rodilla izquierdo (Extendido/Plexado): 120/53
Tobillo izquierdo (Extendido/Plexado): 55/129
Pie izquierdo (Exterior/Apoyo/Interior): 88/71/3
*/

#include <Servo.h>

Servo miservo;  // create servo object to control a servo

const int PinControl=A1; // pin al que está conectado el servomotor
int pos_servo = 90;  // posición del servo entre 0 y 180, inicializado a 90

int valor_serie;    // valor leido por serie

void setup() {
  miservo.attach(PinControl);  
  Serial.begin(9600); // velocidad de envio de datos por serie
}

void loop() {
  if (Serial.available()){
    valor_serie=Serial.read();
    switch (valor_serie){
      case 'a':
        Serial.print("has pulsado a, el valor del servomotor: ");
        pos_servo++;
        Serial.println ("*S"+String(pos_servo)+"*");
        break;
      case 'b':
        Serial.print("has pulsado b, el valor del servomotor: ");
        pos_servo--;
        Serial.println ("*S"+String(pos_servo)+"*");
        break;
    }
  }
  miservo.write(pos_servo);                  // enviar el servo al ángulo indicado
  delay(15);                           // esperar a que el servo alcance la posición
}

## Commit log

2019-04-15 Subida de archivos masivo
2020-01-07 Creacion de lista de materiales para la pcb ESP-BT
2020-01-14 Actualizacion documentacion a version Pacifistabot-ESP
    [PCB_pacifista-B.Cu.gbl, PCB_pacifista-B.Mask.gbs, PCB_pacifista-B.SilkS.gbo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]
2020-01-22 actualización componentes 3D
    [Pacifistabot-ESP-01s.kicad_pcb]
2020-01-31 correccion bugs de la documentacion
    [Configuracion.ino]
2020-05-15 Corrección de los pines de la PCB y el logo de DB
    [Pacifistabot-ESP-01s.kicad_pcb, Pacifistabot-ESP-01s.sch]
2020-06-17 Creación de alhambra
    [PCB_pacifista-2020-06-03-22-14-22.sch, PCB_pacifista-2020-06-12-10-39-09.sch, Pacifistabot-ESP-01s.kicad_pcb]
2020-06-26 Creación de lista de materiales de la PCB AlhambraII
2020-06-26 Actualización de los links de la pcb AlhII
    [FPGA.kicad_pcb, FPGA.sch]
2020-06-26 Corrección fallo de pieza 14 stl
2020-06-26 Subida de los archivos gerbers
    [FPGA-B_Cu.gbr, FPGA-B_Mask.gbr, FPGA-Edge_Cuts.gbr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]
2020-08-31 Subida del pcb freecad tinyfpga
    [Pacifista_TinyFPGA-B_SilkS.dxf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]
